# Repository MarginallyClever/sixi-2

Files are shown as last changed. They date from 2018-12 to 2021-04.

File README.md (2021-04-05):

# Sixi 2 Robot Arm

Sixi 2 is an open source industrial robot arm.  It is designed with six degrees of freedom and can hold 2kg at 80cm.
Some examples of it in action:



## Videos

* https://www.instagram.com/p/B56L99UnWkN/
* https://www.instagram.com/p/B6L7YMTnthS/
* https://www.instagram.com/p/B6jtXw5HbRo/

## Motivation

3D printers can print parts for themselves, but they cannot self-assemble.  The long goal of the Sixi is to build a machine that can assemble copies of itself.

When 3D printers were closed source, they started at $10k.  Makerbot and Prusa changed the game by bringing high quality open source 3D printers down to $2k.  Marginally Clever Robots, Ltd. aims to be the Prusa of robot arms.

## This repository 

This repository contains:

* The STL files from the stable version
* The bill of materials (BOM.csv)
* Issue tickets specifically related to the hardware.
* ROS package.

This repository does NOT contain:

* Assembly instructions + software guide: https://mcr.dozuki.com/c/Sixi_2_kit_Asssembly
* Robot Overlord app to simulate, drive, and test Sixi: https://github.com/MarginallyClever/Robot-Overlord-App
* Makelangelo Firmware in the Sixi's brain: https://github.com/MarginallyClever/Makelangelo-firmware

## Notes

The BOM.csv lists all the parts in the kit, most of which are off-the-shelf.  Some parts are manufactured.
	
	[LSR] laser cut
	[CNC] metal cut on a CNC mill
	[3D]  3D printed PLA plastic.

All the 3D printable parts were produced on a Prusa MK3S.  Parts are carefully designed to have a minimum of support material cleaning.
Please see STLs/STLPrintSettings.csv for recommended layer height, speed, color, etc.

The Sixi has no glue because we like operations that can be undone.

## Collaborate

We love collaborating!  Let's make great things happen together.

* Discuss the project in our Discord: https://discord.gg/p2NRZFxXbh
* For a link to the Fusion files, become one of our Patreon supporters: https://www.patreon.com/imakerobots
* See also the ROS.org wiki page: https://wiki.ros.org/Robots/Sixi

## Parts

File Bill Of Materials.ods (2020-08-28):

SKU | Part name | Image | type | Qty per Sixi | Unit | Buy Link | Alt buy link | Cost | Currency
Sixi2-001 | Standoff m4x6x20 95947A056 | https://imgur.com/KX3Rz3N | fastener | 16 |  | https://www.aliexpress.com/item/33029121480.html |  | $7.58 | cad
Sixi2-002 | Standoff m3x4.5x12 95947A008 | https://imgur.com/IH3mTjJ | fastener | 7 |  | https://www.aliexpress.com/item/33029121480.html |  | $2.85 | cad
Sixi2-003 | Standoff #4-40x7 M-F 93505A101 | https://imgur.com/c1Dago8 | fastener | 4 |  | https://www.mcmaster.com/93505A101
Sixi2-005 | Set Screw m3x4 flatEnd 92605A098 | https://www.mcmaster.com/mvb/library/20130930/92605a098l.gif | fastener | 22 |  | https://www.aliexpress.com/item/32864937826.html
Sixi2-009 | screw M5x20 socket head cap 90128A248 | https://www.mcmaster.com/mvb/library/20140217/90128a248l.gif | fastener | 12 |  | https://www.mcmaster.com/90128a248
Sixi2-012 | screw M4x45 socket head cap partially threaded 91292A133 | https://www.mcmaster.com/mvb/library/20140512/91292a133l.gif | fastener | 36 |  | https://www.mcmaster.com/91292A133
Sixi2-014 | screw M4x25 socket head 91292A122 | https://imgur.com/v1CkgbG | fastener | 28 |  | https://www.mcmaster.com/91292A122 |  | $9.94 | usd
Sixi2-015 | screw M4x14 socket head cap 91292A038 | https://www.mcmaster.com/mvb/library/20140512/91292a038l.gif | fastener | 6 |  | https://www.mcmaster.com/91292a038
Sixi2-016 | screw m3x8 socket head cap 91292A112 | https://www.mcmaster.com/mvb/library/20140512/91292a112l.gif | fastener | 38 |  | https://www.mcmaster.com/91292a112
Sixi2-021 | screw m3x5 socket head cap 91292A110 | https://www.mcmaster.com/mvb/library/20140512/91292a110l.gif | fastener | 42 |  | https://www.mcmaster.com/91292a110
Sixi2-024 | screw m3x45 socket head cap partially threaded 91290A079 | https://imgur.com/NSbllIR | fastener | 59 |  | https://www.mcmaster.com/91290a079 |  | $7.58 | usd
Sixi2-029 | screw m3x35 socket head cap partially threaded 91292A033 | https://www.mcmaster.com/mvb/library/20140512/91292a033l.gif | fastener | 8 |  | https://www.mcmaster.com/91292a033
Sixi2-031 | screw m3x30 socket head cap partially threaded 91292A022 | https://www.mcmaster.com/mvb/library/20140512/91292a022l.gif | fastener | 4 |  | https://www.mcmaster.com/91292a022
Sixi2-033 | screw m3x25 socket head cap partially threaded 91292A020 | https://imgur.com/angOEbH | fastener | 47 |  | https://www.mcmaster.com/91292a020 |  | $7.23 | usd
Sixi2-037 | screw m3x20 socket head cap 91290A123 | https://imgur.com/wMKXFRN | fastener | 28 |  | https://www.mcmaster.com/91292a123 |  | $6.78 | usd
Sixi2-039 | screw m3x16 socket head cap 91292A115 | https://imgur.com/oTCz141 | fastener | 26 |  | https://www.mcmaster.com/91292a115
Sixi2-043 | screw M3x10 socket head cap 91292A113 | https://imgur.com/oTCz141 | fastener | 46 |  | https://www.mcmaster.com/91292a113
Sixi2-047 | screw m2x6 socket head cap 91292A831 | https://imgur.com/oTCz141 | fastener | 52 |  | https://www.mcmaster.com/91292a831
Sixi2-053 | screw m2x12 socket head cap 91292A834 | https://imgur.com/oTCz141 | fastener | 8 |  | https://www.mcmaster.com/91292a834
Sixi2-056 | nut m5 nylock 90576A104 | https://imgur.com/oTCz141 | fastener | 4 |  | https://www.mcmaster.com/90576a104
Sixi2-057 | nut M5 hex 90592A095 | https://imgur.com/oTCz141 | fastener | 20 |  | https://www.mcmaster.com/90592a095
Sixi2-059 | nut m4 nylock 90576A103 | https://imgur.com/oTCz141 | fastener | 10 |  | https://www.mcmaster.com/90576a103
Sixi2-061 | nut M4 hex 90592A090 | https://imgur.com/oTCz141 | fastener | 32 |  | https://www.mcmaster.com/90592a090
Sixi2-063 | nut M3 square DIN 562 | https://imgur.com/oTCz141 | fastener | 30 |  | https://www.aliexpress.com/item/32875607040.html |  | $1.27 | cad
Sixi2-067 | nut m3 nylock 90576A102 | https://imgur.com/oTCz141 | fastener | 116 |  | https://www.mcmaster.com/90576a102
Sixi2-072 | nut m3 hex 90592A085 | https://imgur.com/oTCz141 | fastener | 90 |  | https://www.mcmaster.com/90592a085
Sixi2-078 | nut m2 hex 90592A075 | https://imgur.com/oTCz141 | fastener | 4 |  | https://www.mcmaster.com/90592a075
Sixi2-079 | NEMA24 100mm | https://i.imgur.com/mdeoYVg.jpg | motor | 1 |  | https://www.omc-stepperonline.com/nema-24-stepper-motor/dual-shaft-nema-24-stepper-motor-42a-4nm-566-ozin-60x60x100mm-4-wires-24hs39-4204d.html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 |  | $34.30 | usd
Sixi2-080 | NEMA23 56mm | https://i.imgur.com/GoVljdT.jpg | motor | 2 |  | https://www.omc-stepperonline.com/nema-23-stepper-motor/e-series-nema-23-stepper-motor-bipolar-1-8deg-4-8-nm-679-87oz-in-6-0a-86x86x80mm-4-wires.html |  | $23.92 | usd
Sixi2-082 | NEMA17 48mm | https://i.imgur.com/5FlxOez.jpg | motor | 2 |  | https://www.omc-stepperonline.com/nema-17-stepper-motor/nema-17-bipolar-59ncm-84oz-in-2a-42x48mm-4-wires-w-1m-cable-and-connector.html |  | $18.78 | usd
Sixi2-083 | NEMA17 39mm | https://i.imgur.com/CCPT4R4.jpg | motor | 1 |  | https://www.omc-stepperonline.com/nema-17-stepper-motor/nema-17-bipolar-45ncm-63-74oz-in-1-5a-42x42x39mm-4-wires-w-1m-cable-and-connector.html |  | $8.22 | usd
Sixi2-084 | [LSR] - ABS Junction Box [380x260x105mm] (sold as 15"x10.2"x4.13") | https://imgur.com/rg18C09 |  | 1 |  | https://www.amazon.ca/LeMotech-Waterproof-Dustproof-Universal-Enclosure/dp/B075WZZZ49 | https://www.alibaba.com/product-detail/Waterproof-electrical-box-ABS-solid-cover_60779392408.html | $63.85 | cad
Sixi2-085 | bearing flanged MF83 [3x8x3mm] | https://imgur.com/06VHik1 | bearing | 8 |  | https://www.alibaba.com/product-detail/Sixi-Package-MF83-6813-6809-6708_1600104697831.html |  | $6.85 | cad
Sixi2-086 | bearing 6813 [65x85x10mm] | https://imgur.com/hqhQNOH | bearing | 4 |  | https://www.alibaba.com/product-detail/Sixi-Package-MF83-6813-6809-6708_1600104697831.html |  | $41.32 | cad
Sixi2-088 | bearing 6809 [45x58x7mm] | https://imgur.com/XzdQ307 | bearing | 2 |  | https://www.alibaba.com/product-detail/Sixi-Package-MF83-6813-6809-6708_1600104697831.html |  | $9.93 | cad
Sixi2-089 | bearing 6708 [40x50x6mm] | https://imgur.com/bQkI64m | bearing | 4 |  | https://www.alibaba.com/product-detail/Sixi-Package-MF83-6813-6809-6708_1600104697831.html |  | $22.64 | cad
Sixi2-090 | bearing 6706 [30x37x4mm] | https://imgur.com/hUOlbzJ | bearing | 6 |  | https://www.alibaba.com/product-detail/Sixi-Package-MF83-6813-6809-6708_1600104697831.html |  | $21.66 | cad
Sixi2-092 | bearing 6702 [15x21x4mm] | https://imgur.com/hUOlbzJ | bearing | 9 |  | https://www.alibaba.com/product-detail/Sixi-Package-MF83-6813-6809-6708_1600104697831.html
Sixi2-095 | bearing 6701 [12x18x4mm] | https://imgur.com/hUOlbzJ | bearing | 16 |  | https://www.alibaba.com/product-detail/Sixi-Package-MF83-6813-6809-6708_1600104697831.html |  | $5.93 | cad
Sixi2-099 | [RAW] - Dupont Housing 7pin | https://d3s11pzv7w3h1q.cloudfront.net/wp-content/uploads/CN-DU-H07.jpg | electrical conn | 7 |  | https://www.aliexpress.com/item/33035707563.html?spm=a2g0o.cart.0.0.6c9f3c00vk0l6Z&mp=1
Sixi2-100 | [RAW] - 40-pin Ribbon Cable pitch 1.27 {4 sets of 10 pin} - [3000mm] | https://imgur.com/TS6cFpq | electrical wire | 1 |  | https://www.aliexpress.com/item/4000007978134.html |  | $12.03 | cad
Sixi2-101 | [MISC] - Timing Belt GT2-6 [400mm] | https://i.imgur.com/uhfbEJQ.jpg | timing belt | 1 |  | https://www.aliexpress.com/item/1858498241.html?spm=2114.12010612.8148356.27.54897861M6BUJx
Sixi2-102 | [MISC] - Timing Belt GT2-6 [336mm] | https://i.imgur.com/JaAKgMa.jpg | timing belt | 2 |  | https://www.aliexpress.com/item/1858543592.html?spm=2114.12010612.8148356.31.54897861M6BUJx
Sixi2-104 | [MISC] - Timing Belt GT2-6 [160mm] | https://i.imgur.com/64wMtBN.jpg | timing belt | 3 |  | https://www.aliexpress.com/item/4000034068206.html?spm=2114.12010612.8148356.33.54897861M6BUJx
Sixi2-105 | [MISC] - Braided Cable Sleeve (16mm dia) [900mm] | https://imgur.com/uPXoAG2 |  | 1 |  | https://www.aliexpress.com/item/4000279970497.html
Sixi2-106 | [MECH] - GT2 Pulley 20t-5mm | https://imgur.com/e1Oz3dD |  | 3 |  | https://www.aliexpress.com/item/32852674549.html
Sixi2-107 | [LSR] - PSU Mounting Plate - {Acrylic} |  | laser cut | 1 |  | source material: associated plastics
Sixi2-108 | [LSR] - PicassoCoverPlate - {Acrylic} |  | laser cut | 2 |  | source material: associated plastics
Sixi2-109 | [LSR] - MountingBoard [250mmx300mm] |  | laser cut | 1 |  | source material: associated plastics
Sixi2-110 | [LSR] - ForkSensSide - {Acrylic} |  | laser cut | 1 |  | source material: associated plastics
Sixi2-111 | [LSR] - ForkGBSide - {Acrylic} |  | laser cut | 1 |  | source material: associated plastics
Sixi2-112 | [ELEC] - sensor AS5147 {straight header pins on label side} | https://imgur.com/sKfHzqC |  | 1 |  | https://www.digikey.ca/en/products/detail/ams/AS5147-TS-EK-AB/5452350 |  | $108.67 | cad
Sixi2-113 | [ELEC] - sensor AS5147 {right-angle header pins on label side} |  |  | 2 |  | https://www.digikey.ca/en/products/detail/ams/AS5147-TS-EK-AB/5452350
Sixi2-114 | [ELEC] - sensor AS5147 {right-angle header pins on chip side} |  |  | 3 |  | https://www.digikey.ca/en/products/detail/ams/AS5147-TS-EK-AB/5452350
Sixi2-118 | [RAW] - Screw Terminal 4P-3.5mm |  | electrical conn | 6 |  | https://www.aliexpress.com/item/32981258851.html
Sixi2-119 | [RAW] - Screw Terminal 8p-2.54mm |  | electrical conn | 6 |  | https://www.aliexpress.com/item/32939185688.html | https://www.digikey.ca/en/products/detail/on-shore-technology-inc/OSTVN08A150/1588868 | $10.16 | cad
Sixi2-121 | [RAW] - Screw Terminal 4p-2.54mm |  | electrical conn | 1 |  | https://www.aliexpress.com/item/32939185688.html
Sixi2-122 | [RAW] - Screw Terminal 2P-5mm |  | electrical conn | 1 |  | https://www.aliexpress.com/item/32799616010.html
Sixi2-123 | [RAW] - ROCKER SWITCH W/ IEC SOCKET & FUSE HOLDER (SCREW) | https://imgur.com/jIWw7tJ |  | 1 |  | https://www.aliexpress.com/item/32957627591.html |  | $2.17 | cad
Sixi2-124 | [ELEC] - Power Supply 24V-20A | https://imgur.com/Z2UQoKd |  | 1 |  | https://www.aliexpress.com/item/33024871217.html?currency=CAD&createTmp=1&cur_warehouse=CN |  | $29.80 | cad
Sixi2-125 | [RAW] - PCB PanelAdpater | https://imgur.com/q5Lh6uE |  | 3 |  | https://oshpark.com/projects/Xrd8Wjid/order
Sixi2-126 | [RAW] - PCB MegaShield | https://imgur.com/dRTLl7Z |  | 1 |  | https://oshpark.com/projects/pKP4QArV/order
Sixi2-127 | [ELEC] - USB-B M/F Panel Mount Extension | https://imgur.com/UnHMrv1 | electrical wire | 1 |  | https://www.aliexpress.com/item/32862578019.html |  | $1.62 | cad
Sixi2-128 | [RAW] - NPN Transistor 2N2222A |  |  | 9 |  | https://leeselectronic.com/en/product/7174.html
Sixi2-129 | [RAW] - Voltage Regulator MP1584EN |  |  | 2 |  | https://www.aliexpress.com/item/32898137328.html
Sixi2-130 | [ELEC] - magnet 8x2.5mm neodynium | https://imgur.com/sKfHzqC |  | 6 |  | Comes with AS5147
Sixi2-135 | [ELEC] - D-SUB F-Conn IDC DC-37 | https://imgur.com/c1Dago8 | electrical conn | 1 |  | https://www.aliexpress.com/item/32975383933.html | https://www.digikey.ca/en/products/detail/cw-industries/CWR-281-37-0000/59402
Sixi2-136 | [RAW] - D-SUB F-Conn right-angle DC-37 | https://imgur.com/c1Dago8 | electrical conn | 1 |  | https://www.aliexpress.com/item/32507743539.html
Sixi2-137 | [ELEC] - D-SUB M/M 1m Cable DC-37 | https://imgur.com/WCuU4bf | electrical wire | 1 |  | https://www.aliexpress.com/item/4000107157121.html |  | $5.55 | cad
Sixi2-138 | [ELEC] - Stepper Driver DM556T | https://imgur.com/uFXRD0P |  | 1 |  | https://www.omc-stepperonline.com/digital-stepper-driver-18~56a-20-50vdc-for-nema-23-24-34-stepper-motor-dm556t.html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 |  | $38.16 | usd
Sixi2-139 | [ELEC] - Stepper Driver DM542T | https://imgur.com/FjPGjfd |  | 2 |  | https://www.omc-stepperonline.com/digital-stepper-driver-10-42a-20-50vdc-for-nema-17-23-24-stepper-motor-dm542t.html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 |  | $32.29 | usd
Sixi2-140 | [ELEC] - Stepper Driver DM320T | https://imgur.com/IgUOxMS |  | 3 |  | https://www.omc-stepperonline.com/digital-stepper-driver-03-22a-18-30vdc-for-nema-8-11-14-16-17-stepper-motor-dm320t.html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 |  | $20.55 | usd
Sixi2-141 | [ELEC] - Aviation GX16-8p Cable F/F - [1000mm] | https://imgur.com/eAqFwsP | electrical wire | 4 |  | https://www.aliexpress.com/item/32840461595.html?spm=2114.12010612.8148356.41.33fb6dccKnZkSS |  | $82.15 | cad
Sixi2-142 | [RAW] - Aviation GX16-8p Plug | https://imgur.com/E9g45bx | electrical conn | 4 |  | https://www.aliexpress.com/item/32865925885.html?spm=2114.12010608.0.0.47a735f2P9IyrY |  | $5.71 | cad
Sixi2-142 | [RAW] - Aviation GX16-8p Plug |  | electrical conn | 4 |  | https://www.aliexpress.com/item/32865925885.html?spm=2114.12010608.0.0.47a735f2P9IyrY
Sixi2-143 | [ELEC] - Arduino Mega 2650 | https://imgur.com/XMHnerM |  | 1 |  | https://www.aliexpress.com/item/32850843888.html |  | $11.36 | cad
Sixi2-144 | [ELEC] - 4x22AWG {M5} - [225mm] |  | assembly | 1 |  | https://leeselectronic.com/en/product/21134.html
Sixi2-145 | [ELEC] - 4x22AWG {M4} - [185mm] |  | assembly | 1 |  | https://leeselectronic.com/en/product/21134.html
Sixi2-146 | [ELEC] - 4x22AWG {M2} - [200mm] |  | assembly | 1 |  | https://leeselectronic.com/en/product/21134.html
Sixi2-147 | [ELEC] - 4x22AWG {M0/1} - [210mm] |  | assembly | 2 |  | https://leeselectronic.com/en/product/21134.html
Sixi2-148 | [ELEC] - 4x22AWG {M3} - [165mm] |  | assembly | 1 |  | https://leeselectronic.com/en/product/21134.html
Sixi2-149 | [SUB] - 2x18AWG {Switch Jumper} - [65mm] |  | assembly | 1 |  | https://leeselectronic.com/en/product/2118182.html
Sixi2-150 | [ELEC] - 2x22AWG {PSU - Small Drivers} - [335mm] |  | assembly | 1 |  | https://leeselectronic.com/en/product/22304.html
Sixi2-151 | [ELEC] - 2x22AWG {PSU - Arduino} - [420mm] |  | assembly | 1 |  | https://leeselectronic.com/en/product/22304.html
Sixi2-152 | [ELEC] - 2x18AWG {PSU - Big Drivers} - [160mm] |  | assembly | 1 |  | https://leeselectronic.com/en/product/2118182.html
Sixi2-154 | [RAW] - 3x16AWG Power Cord - 365mm {Switch to PSU} |  | electrical wire | 1 |  | https://leeselectronic.com/en/product/27773.html
Sixi2-155 | [ELEC] - 6-pin Ribbon Cable F/O - Brown to Blue {sensor 2 Elbow} - [890mm] |  | assembly | 1 |  | https://leeselectronic.com/en/product/2287.html
Sixi2-156 | [ELEC] - 6-pin Ribbon Cable F/O - Brown to Blue {sensor 1 Shoulder} - [365mm] |  | assembly | 1 |  | https://leeselectronic.com/en/product/2287.html
Sixi2-157 | [ELEC] - 6-pin Ribbon Cable F/F - Brown to Blue {sensor 5 Hand Ext.} - [210mm] |  | assembly | 1 |  | https://leeselectronic.com/en/product/2287.html
Sixi2-158 | [ELEC] - 6-pin Ribbon Cable F/O - Brown to Blue {sensor 4 Wrist} - [1520mm] |  | assembly | 1 |  | https://leeselectronic.com/en/product/2287.html
Sixi2-159 | [ELEC] - 6-pin Ribbon Cable M/O - Brown to Blue {sensor 5 Hand} - [1470mm] |  | assembly | 1 |  | https://leeselectronic.com/en/product/2287.html
Sixi2-160 | [ELEC] - 6-pin Ribbon Cable F/O - Brown to Blue {sensor 0 Anchor} - [145mm] |  | assembly | 1 |  | https://leeselectronic.com/en/product/2287.html
Sixi2-161 | [ELEC] - 6-pin Ribbon Cable F/O - Brown to Blue {sensor 3 Ulna} - [1160mm] |  | assembly | 1 |  | https://leeselectronic.com/en/product/2287.html
Sixi2-162 | [CNC] - Tube Brass [7/32in x 492mm] | https://imgur.com/Z13f9Rq | cnc | 1 |  |  |  | $7.95 | cad
Sixi2-163 | [CNC] - Tube Brass [7/32in x 25.95mm] {wrist shaft} | https://imgur.com/1g44VEV | cnc | 1
Sixi2-164 | [CNC] - Tube Brass [5/16in x 452.6mm] | https://imgur.com/VDGTeUY | cnc | 1 |  |  |  | $10.99 | cad
Sixi2-165 | [CNC] - Tube Brass [5/16in x 19.5mm] {hand shaft} | https://imgur.com/DENvd4o | cnc | 1
Sixi2-166 | [CNC] - Tube Brass [3/8in x 76.5mm] {wrist sensor shaft} | https://imgur.com/8zaq0Lm | cnc | 1 |  |  |  | $12.50 | cad
Sixi2-167 | [CNC] - Tube Brass [3/8in x 396.35mm] | https://imgur.com/YqrMDTm | cnc | 1
Sixi2-168 | [CNC] - Tube Brass [1/8in x 520mm] {ulna sensor shaft} | https://imgur.com/7tEXEqR | cnc | 1 |  |  |  | $5.25 | cad
Sixi2-169 | [CNC] - Tube Brass [1/8in x 35mm] {hand sensor shaft} | https://imgur.com/Fj52HuV | cnc | 1
Sixi2-170 | [CNC] - Pipe Aluminum [1.375in x 360.25mm] | https://imgur.com/DYVS192 | cnc | 1 |  |  |  | $23.13 | cad
Sixi2-171 | [CNC] - Pipe Aluminum [1.375in x 260.25mm] | https://imgur.com/Qf2uR6f | cnc | 1 |  |  |  | $16.69 | cad
Sixi2-172 | dowel pin steel 91595A130 - [3x24mm] | https://imgur.com/OpPEaqS | fastener | 77 |  | https://www.aliexpress.com/item/4000176913597.html |  | $12.30 | cad
Sixi2-174 | [CNC] - Tube Brass [3.5mm x 18.5mm] {GB inner rollers} | https://imgur.com/ebuiq8H | cnc | 24 |  |  |  | $4.45 | cad
Sixi2-176 | [3D] - xSAb-AS5147 SensorAdapter2.stl |  | 3d printed | 3
Sixi2-179 | [3D] - xSAa-AS5147 SensorAdapter1.stl |  | 3d printed | 2
Sixi2-181 | [3D] - 7E-plug wall adapter.stl |  | 3d printed | 1
Sixi2-182 | [3D] - 7Db-ArduinoTray.stl |  | 3d printed | 1
Sixi2-183 | [3D] - 7Da-ArduinoStandoff.stl |  | 3d printed | 1
Sixi2-184 | [3D] - 7C-stepperDriverAdapter 542.stl |  | 3d printed | 1
Sixi2-185 | [3D] - 7B-stepperDriverAdapter 556-542.stl |  | 3d printed | 1
Sixi2-186 | [3D] - 7A-stepperDriverAdapter 320x3.stl |  | 3d printed | 1
Sixi2-187 | [3D] - 6PI-pulleyInterior OUTPUT-64t v12.stl |  | 3d printed | 1
Sixi2-188 | [3D] - 6PE-pulleyExterior OUTPUT-63t v7.stl |  | 3d printed | 1
Sixi2-189 | [3D] - 6Md-SensorMagHolder.stl |  | 3d printed | 1
Sixi2-190 | [3D] - 6Mc-WristMagHolder v7.stl |  | 3d printed | 1
Sixi2-191 | [3D] - 6Ea-rotorTOP.stl |  | 3d printed | 1
Sixi2-192 | [3D] - 6Ea-rotorBOTT.stl |  | 3d printed | 1
Sixi2-193 | [3D] - 6Ea-HousingTOP.stl |  | 3d printed | 1
Sixi2-194 | [3D] - 6Ea-HousingBOTT.stl |  | 3d printed | 1
Sixi2-195 | [3D] - 6Ea-eShaftTOP.stl |  | 3d printed | 1
Sixi2-196 | [3D] - 6Ea-eShaftBOTT.stl |  | 3d printed | 1
Sixi2-197 | [3D] - 6Db-BevelGear OUTPUT-20t.stl |  | 3d printed | 1
Sixi2-198 | [3D] - 6Da-rotorTOP.stl |  | 3d printed | 1
Sixi2-199 | [3D] - 6Da-rotorBOTT.stl |  | 3d printed | 1
Sixi2-200 | [3D] - 6Da-outputDiskTOP.stl |  | 3d printed | 1
Sixi2-201 | [3D] - 6Da-outputDiskBOTT.stl |  | 3d printed | 1
Sixi2-202 | [3D] - 6Da-HousingTOP.stl |  | 3d printed | 1
Sixi2-203 | [3D] - 6Da-HousingBOTT.stl |  | 3d printed | 1
Sixi2-204 | [3D] - 6Da-Hand.stl DEPRECATED |  | 3d printed | 1
Sixi2-205 | [3D] - 6Da-eShaftTOP.stl |  | 3d printed | 1
Sixi2-206 | [3D] - 6Da-eShaftBOTT.stl |  | 3d printed | 1
Sixi2-207 | [3D] - 6Bc-bearingSpacer v3.stl |  | 3d printed | 1
Sixi2-208 | [3D] - 6Ba-BevelGear INPUT-20t v13.stl |  | 3d printed | 1
Sixi2-209 | [3D] - 6Ae-SensHolder.stl |  | 3d printed | 1
Sixi2-210 | [3D] - 6Ad-wristGBDiskBott.stl |  | 3d printed | 1
Sixi2-211 | [3D] - 6Ac-wristGBDiskTop.stl |  | 3d printed | 1
Sixi2-212 | [3D] - 6Ab-PicassoTop.stl |  | 3d printed | 1
Sixi2-213 | [3D] - 6Aa-PicassoBottom.stl |  | 3d printed | 1
Sixi2-214 | [3D] - 5PI - pulleyInterior INPUT-64t v7.stl |  | 3d printed | 1
Sixi2-215 | [3D] - 5PE - pulleyExterior INPUT-63t v7.stl |  | 3d printed | 1
Sixi2-216 | [3D] - 5I - Idler BearingCoverHalf.stl |  | 3d printed | 8
Sixi2-217 | [3D] - 5Bd - outputDiskTOP.stl |  | 3d printed | 1
Sixi2-218 | [3D] - 5Bd - outputDiskMID.stl |  | 3d printed | 1
Sixi2-219 | [3D] - 5Bd - outputDiskBOTT.stl |  | 3d printed | 1
Sixi2-220 | [3D] - 5Bc - housingTOP2.stl |  | 3d printed | 1
Sixi2-221 | [3D] - 5Bc - housingTOP1.stl |  | 3d printed | 1
Sixi2-222 | [3D] - 5Bb - housingMID.stl |  | 3d printed | 1
Sixi2-223 | [3D] - 5Ba - housingBOTT2.stl |  | 3d printed | 1
Sixi2-224 | [3D] - 5Ba - housingBOTT1.stl |  | 3d printed | 1
Sixi2-225 | [3D] - 5B - shaftCAP.stl |  | 3d printed | 1
Sixi2-226 | [3D] - 5B - rotorTOP.stl |  | 3d printed | 1
Sixi2-227 | [3D] - 5B - rotorBOTT.stl |  | 3d printed | 1
Sixi2-228 | [3D] - 5B - eShaftTOP.stl | https://imgur.com/RXKgI3l | 3d printed | 1
Sixi2-229 | [3D] - 5B - eShaftBOTT.stl | https://imgur.com/LiqzP7j | 3d printed | 1
Sixi2-230 | [3D] - 5Ac - CableClamp.stl | https://imgur.com/9ks011I | 3d printed | 1
Sixi2-231 | [3D] - 5Ab - UlnaSensRod.stl | https://imgur.com/0YdJMmV | 3d printed | 1
Sixi2-232 | [3D] - 5Aa - ForkTop.stl |  | 3d printed | 1
Sixi2-233 | [3D] - 5Aa - ForkBottom.stl |  | 3d printed | 1
Sixi2-234 | [3D] - 4S-Sixi spacer v8.stl | https://imgur.com/ebuiq8H | 3d printed | 1
Sixi2-235 | [3D] - 4Pe-pulley7-32in OUTPUT-30t.stl |  | 3d printed | 1
Sixi2-236 | [3D] - 4Pd-pulley5-16in OUTPUT-30t.stl |  | 3d printed | 1
Sixi2-237 | [3D] - 4Pc-pulley3-8in OUTPUT-30t.stl |  | 3d printed | 1
Sixi2-238 | [3D] - 4MB-UlnaMagBearing.stl |  | 3d printed | 1
Sixi2-239 | [3D] - 4M-UlnaMagHolder.stl |  | 3d printed | 1
Sixi2-240 | [3D] - 4B-MotorMount.stl |  | 3d printed | 3
Sixi2-241 | [3D] - 4Ab-ElbowTail.stl |  | 3d printed | 1
Sixi2-242 | [3D] - 4Aa-ElbowTail.stl |  | 3d printed | 1
Sixi2-243 | [3D] - 3R-rotorTOPScrew.stl |  | 3d printed | 1
Sixi2-244 | [3D] - 3R-rotorTOPNut.stl |  | 3d printed | 1
Sixi2-245 | [3D] - 3R-rotorBOTTScrew.stl |  | 3d printed | 1
Sixi2-246 | [3D] - 3R-rotorBOTTNut.stl |  | 3d printed | 1
Sixi2-247 | [3D] - 3Mc-ElbowMagHolderCap.stl |  | 3d printed | 1
Sixi2-248 | [3D] - 3MB-ElbowMagBearing.stl |  | 3d printed | 1
Sixi2-249 | [3D] - 3M-ElbowMagHolder.stl |  | 3d printed | 1
Sixi2-250 | [3D] - 3GB-shaftSensMid.stl |  | 3d printed | 1
Sixi2-251 | [3D] - 3GB-shaftCoupler.stl |  | 3d printed | 1
Sixi2-252 | [3D] - 3GB-shaftCap - SEN.stl |  | 3d printed | 1
Sixi2-253 | [3D] - 3GB-shaftCap - MOTT.stl |  | 3d printed | 1
Sixi2-254 | [3D] - 3GB-eShaft.stl |  | 3d printed | 1
Sixi2-255 | [3D] - 3GB-elbowTOPcap.stl |  | 3d printed | 1
Sixi2-256 | [3D] - 3GB-elbowTOP - SEN.stl |  | 3d printed | 1
Sixi2-257 | [3D] - 3GB-elbowTOP - MOT.stl |  | 3d printed | 1
Sixi2-258 | [3D] - 3GB-elbowBottCap - SEN.stl |  | 3d printed | 1
Sixi2-259 | [3D] - 3GB-elbowBottCap - MOT.stl |  | 3d printed | 1
Sixi2-260 | [3D] - 3GB-elbowBOTT - SEN.stl |  | 3d printed | 1
Sixi2-261 | [3D] - 3GB-elbowBOTT - MOT.stl |  | 3d printed | 1
Sixi2-262 | [3D] - 2R-rotorTOPScrew.stl |  | 3d printed | 1
Sixi2-263 | [3D] - 2R-rotorTOPNut.stl |  | 3d printed | 1
Sixi2-264 | [3D] - 2R-rotorBOTTScrew.stl |  | 3d printed | 1
Sixi2-265 | [3D] - 2R-rotorBOTTNut.stl |  | 3d printed | 1
Sixi2-266 | [3D] - 2MB-ShoulderMagBearing.stl |  | 3d printed | 1
Sixi2-267 | [3D] - 2M-ShoulderMagHolder.stl |  | 3d printed | 1
Sixi2-268 | [3D] - 2GB-shoulderTopCap - SEN.stl |  | 3d printed | 1
Sixi2-269 | [3D] - 2GB-shoulderTopCap - MOT.stl |  | 3d printed | 1
Sixi2-270 | [3D] - 2GB-shoulderTOP - SEN.stl |  | 3d printed | 1
Sixi2-271 | [3D] - 2GB-shoulderTOP - MOT.stl |  | 3d printed | 1
Sixi2-272 | [3D] - 2GB-shoulderBOTT - SEN.stl |  | 3d printed | 1
Sixi2-273 | [3D] - 2GB-shoulderBOTT - MOT.stl |  | 3d printed | 1
Sixi2-274 | [3D] - 2GB-shaftCoupler.stl |  | 3d printed | 1
Sixi2-275 | [3D] - 2GB-shaftCap - SEN.stl |  | 3d printed | 1
Sixi2-276 | [3D] - 2GB-shaftCap - MOT.stl |  | 3d printed | 1
Sixi2-277 | [3D] - 2GB-shaftBott.stl |  | 3d printed | 1
Sixi2-278 | [3D] - 2GB-eShaft.stl |  | 3d printed | 1
Sixi2-279 | [3D] - 1PO-pulleyAnchor OUTPUT-71t v6.stl |  | 3d printed | 1
Sixi2-280 | [3D] - 1PI-pulleyAnchor INPUT-71t v7.stl |  | 3d printed | 1
Sixi2-281 | [3D] - 1MB-AnchorMagBearing.stl |  | 3d printed | 1
Sixi2-282 | [3D] - 1M-AnchorMagHolder.stl |  | 3d printed | 1
Sixi2-283 | [3D] - 1GB-shaftTop.stl |  | 3d printed | 1
Sixi2-284 | [3D] - 1GB-shaftEccentric.stl |  | 3d printed | 1
Sixi2-285 | [3D] - 1GB-shaftBott.stl |  | 3d printed | 1
Sixi2-286 | [3D] - 1GB-rotorTOP.stl |  | 3d printed | 1
Sixi2-287 | [3D] - 1GB-rotorBOTT.stl |  | 3d printed | 1
Sixi2-288 | [3D] - 1GB-outputTopDisk.stl |  | 3d printed | 1
Sixi2-289 | [3D] - 1GB-outputTopBearing.stl |  | 3d printed | 1
Sixi2-290 | [3D] - 1GB-outputBottDiskTop.stl |  | 3d printed | 1
Sixi2-291 | [3D] - 1GB-outputBottDiskBott.stl |  | 3d printed | 1
Sixi2-292 | [3D] - 1E-M5x8mm Spacer v3.stl |  | 3d printed | 4
Sixi2-293 | [3D] - 1D-ShoulderMount.stl |  | 3d printed | 1
Sixi2-294 | [3D] - 1C-PanelMount.stl |  | 3d printed | 1
Sixi2-295 | [3D] - 1Bb-AnchorRearBottom.stl |  | 3d printed | 1
Sixi2-296 | [3D] - 1Ba-AnchorFrontBottom.stl |  | 3d printed | 1
Sixi2-297 | [3D] - 1Ab-AnchorMotorHolder.stl | https://imgur.com/8JFypvg | 3d printed | 1
Sixi2-298 | [3D] - 1Aa-AnchorTopSpacer.stl | https://imgur.com/aI7XwZJ | 3d printed | 1
Sixi2-299 | [3D] - 1Aa-AnchorTopBearing.stl | https://imgur.com/6mbvk0M | 3d printed | 1
Sixi2-300 | [3D] - 1Aa-AnchorGearBox.stl | https://imgur.com/7G8Ddya | 3d printed | 1
Sixi2-301 | [CNC] - 1PI-AnchorMotorShaftAdapter |  | cnc | 1 |  | Source material: Metal Super Market
Sixi2-302 | [ELEC] - PSU NEMA-15 power cable 8' |  | electrical wire | 1 |  | https://leeselectronic.com/en/product/17173.html
Sixi2-303 | [RAW] - Dupont Crimp Pins Male | https://a.pololu-files.com/picture/0J2474.1200.jpg?4dc0f8e99610600815a0e4e234f36ce4 | electrical conn | 6 |  | https://www.aliexpress.com/item/32800176540.html |  | $0.94 | cad
Sixi2-304 | [RAW] - Dupont Crimp Pins Female | https://a.pololu-files.com/picture/0J2472.1200.jpg?aed52aea0a6dd376369a345d987c5ad1 | electrical conn | 36 |  | https://www.aliexpress.com/item/32912119601.html |  | $2.10 | cad
Sixi2-305 | [ELEC] - 3-pin Servo Extension Cable M/F - [1000mm] |  |  | 2 |  | https://www.aliexpress.com/item/32986331693.html
Sixi2-306 | [RAW] - Acrylic Sheet {clear} [0.125"x24"x24"] |  |  | 2 |  | Associated Plastics
Sixi2-307 | [RAW] - Pipe Aluminum [1.375in x 361mm] (sold as 1-3/8" dia) |  |  | 1 |  | Metal Supermarket
Sixi2-308 | [RAW] - Pipe Aluminum [1.375in x 261mm] (sold as 1-3/8" dia) |  |  | 1 |  | Metal Supermarket
Sixi2-309 | [RAW] - Aluminum Block [51x 51 x 9.7mm] |  |  | 1 |  | Metal Supermarket
Sixi2-310 | [RAW] - Tube Brass [7/32in x 900mm] |  |  | 1 |  | Magic Box Hobbies
Sixi2-311 | [RAW] - Tube Brass [5/16in x 900mm] |  |  | 1 |  | Magic Box Hobbies
Sixi2-312 | [RAW] - Tube Brass [3/8in x 900mm] |  |  | 1 |  | Magic Box Hobbies
Sixi2-313 | [RAW] - Tube Brass [1/8in x 900mm] |  |  | 1 |  | Magic Box Hobbies
Sixi2-314 | [RAW] - Tube Brass [3.5mm x 300mm] |  |  | 2 |  | Magic Box Hobbies
Sixi2-315 | [ELEC] - 2x22AWG {Small Drivers} - [65mm] |  | assembly | 2
Sixi2-316 | [ELEC] - 2x18AWG {Big Drivers} - [110mm] |  | assembly | 2
Sixi2-317 | [ELEC] - 1x22AWG {Big Drivers} - [30mm] |  | assembly | 6
Sixi2-318 | [MISC] - Velcro Wrap [150mm] |  |  | 2 |  | https://www.aliexpress.com/item/4000916758690.html
Sixi2-319 | [ELEC] - PCB Panel Adapter {assembled} |  | assembly | 3
Sixi2-320 | [ELEC] - PCB Mega Shield {assembled} |  | assembly | 1
Sixi2-321 | [ELEC] - Aviation GX16-8p Cable M/O {TOOL} - [190mm] |  | assembly | 1
Sixi2-322 | [ELEC] - Aviation GX16-8p Cable M/O {M4-340mm & M5-310mm} |  | assembly | 1
Sixi2-323 | [ELEC] - Aviation GX16-8p Cable M/O {M2-370mm & M3-270mm} |  | assembly | 1
Sixi2-324 | [ELEC] - Aviation GX16-8p Cable M/O {M0-370mm & M1-370mm} |  | assembly | 1
Sixi2-325 | [ELEC] - Aviation GX16-8p Cable M/O - {Anchor PCB} [45mm x 2] |  | assembly | 3
Sixi2-326 | [ELEC] - Aviation GX16-8p Cable M/M {other end 4 pin dupont} - [80mm] |  | assembly | 1
Sixi2-327 | [RAW] - Sensor AS5147 |  |  | 6 |  | https://ams.com/as5147
Sixi2-328 | [RAW] - Jumper 1x2pin - 2.54mm |  | electrical conn | 3 |  | https://leeselectronic.com/en/product/2679.html
Sixi2-329 | [RAW] - Header Pins {M-straight} Single Row, pitch 2.54mm |  | electrical conn | 78 | pins | https://leeselectronic.com/en/product/21361.html
Sixi2-330 | [RAW] - Header Pins {M-straight} Double Row, pitch 2.54mm |  | electrical conn | 18 | pins | https://leeselectronic.com/en/product/21362.html
Sixi2-331 | [RAW] - Header Pins {M-right-angle} Single Row, pitch 2.54mm |  | electrical conn | 40 | pins | https://leeselectronic.com/en/product/2149.html
Sixi2-332 | [RAW] - 4x22AWG Threaded Cable [Red, Black, Green & Blue] |  | electrical wire | 1 | mm | https://leeselectronic.com/en/product/21134.html
Sixi2-333 | [RAW] - 2x22AWG Threaded Cable [Red & Black] |  | electrical wire | 1 | mm | https://leeselectronic.com/en/product/22304.html
Sixi2-334 | [RAW] - 2x18AWG Threaded Cable [Red & Black] |  | electrical wire | 1 | mm | https://leeselectronic.com/en/product/211816.html
Sixi2-335 | [RAW] - 1x22AWG Solid Cable [Black] |  | electrical wire | 1 | mm | https://leeselectronic.com/en/product/225060.html
Sixi2-336 | [ELEC] - 3x18AWG Main switch assembly |  | assembly | 1
Sixi2-337 | [RAW] - 4x18AWG Threaded Cable [Red, Black, Green & White] |  | electrical wire |  | mm | https://leeselectronic.com/en/product/211824.html
Sixi2-338 | [RAW] - Wood Sheet Birch Ply [0.125"x24"x24"] |  |  | 1 |  | Windsor Ply
Sixi2-339 | [RAW] - 6-pin Jumper Wire F/F - Brown to Blue [210mm] |  |  | 6 | pins
Sixi2-340 | [RAW] - 3d printer filament, yellow |  |  | 2 | kg | https://www.amazon.ca/1-75mm-Yellow-PLA-Printer-Filament/dp/B01CX9MOK4
Sixi2-341 | [3D] - Hand DIN EN ISO 9409-1-50-4-M6 v11 |  | 3d printed | 1

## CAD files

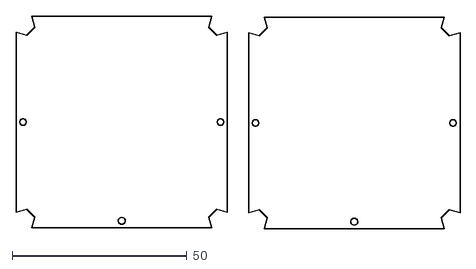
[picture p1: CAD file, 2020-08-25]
LSR/PicassoBoxCover_DXF_INKED.dxf
127.2 x 60.8

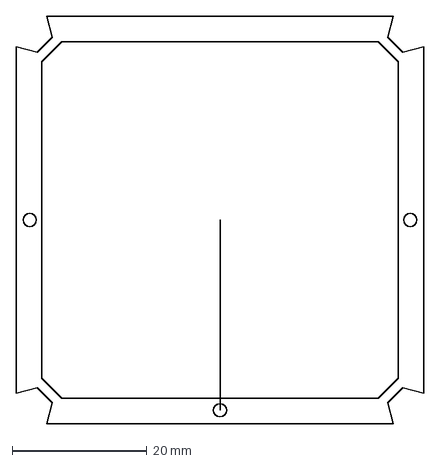
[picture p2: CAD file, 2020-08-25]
LSR/Un_INKED/PicassoBoxCover_DXF.dxf
60.6 x 60.6 mm

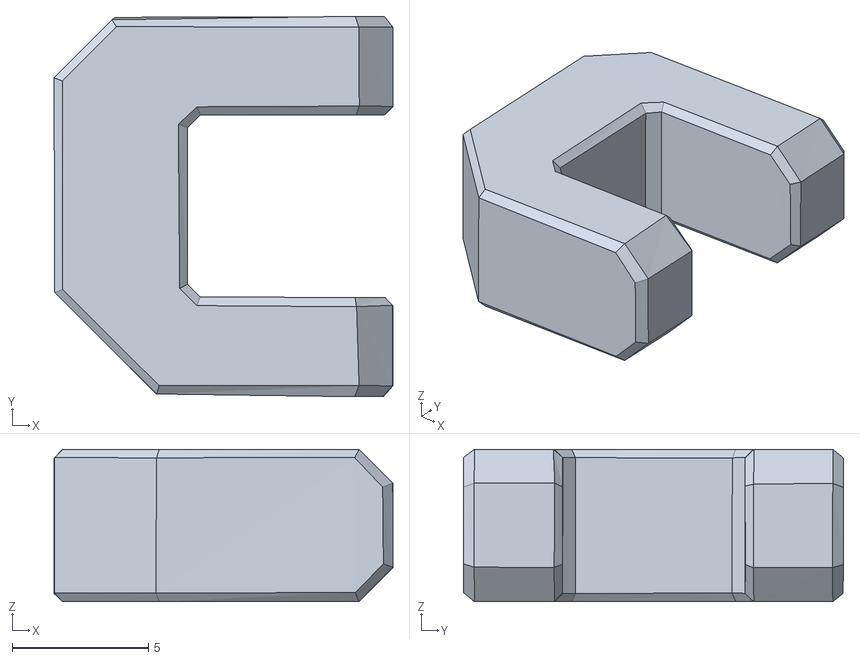
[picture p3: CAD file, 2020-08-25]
ROSPackage/meshes/5_TuningFork.obj
12.5 x 14.0 x 5.60

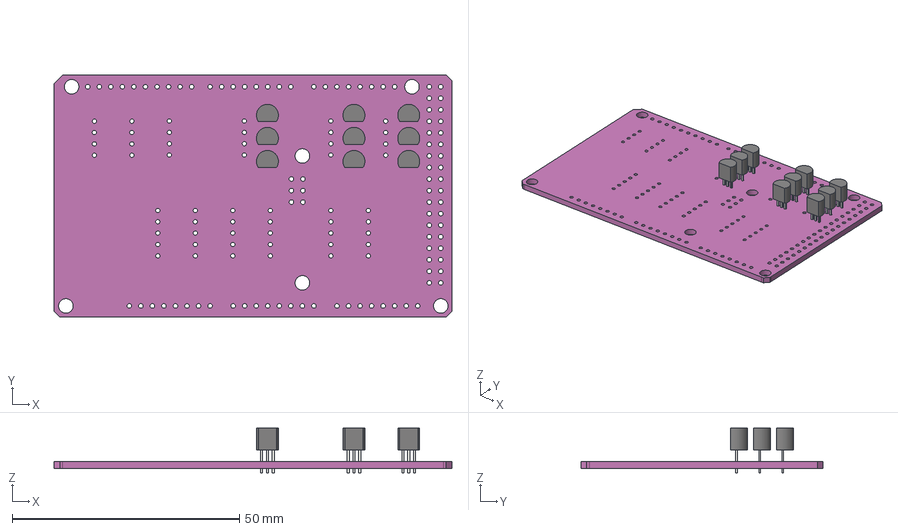
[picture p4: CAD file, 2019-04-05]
sixi2-mega-shield/sixi2-mega-shield.step
87.6 x 53.3 x 9.80 mm
Pcb
PCB_Sketch
Q30_TO-92_Inline_Narrow_5C8B03A0
Q31_TO-92_Inline_Narrow_5C8B03B2
Q32_TO-92_Inline_Narrow_5C8B03C4
Q40_TO-92_Inline_Narrow_5C8B03D6
Q41_TO-92_Inline_Narrow_5C8B03E8
Q42_TO-92_Inline_Narrow_5C8B03FA
Q50_TO-92_Inline_Narrow_5C8B040C
Q51_TO-92_Inline_Narrow_5C8B041E
Q52_TO-92_Inline_Narrow_5C8B0430

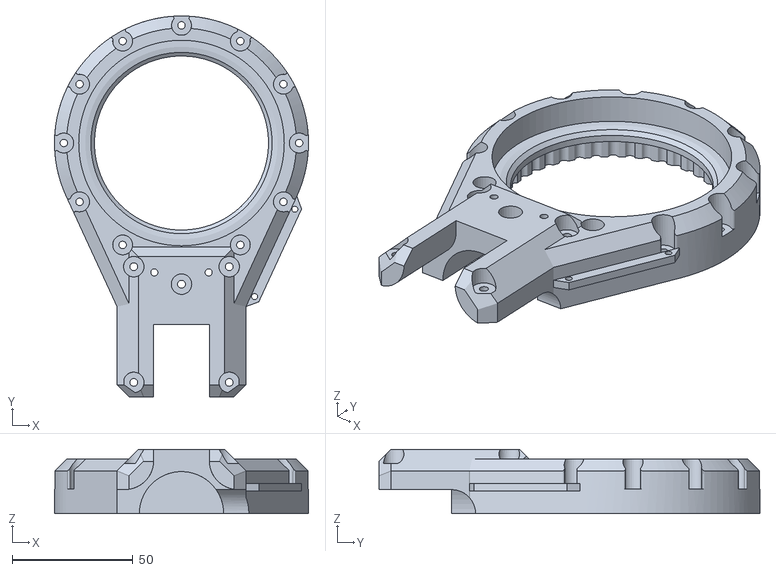
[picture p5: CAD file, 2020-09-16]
STLs/SIXI2-270 [3D] - 2GB-shoulderTOP - SEN.stl
105.2 x 157.7 x 26.7

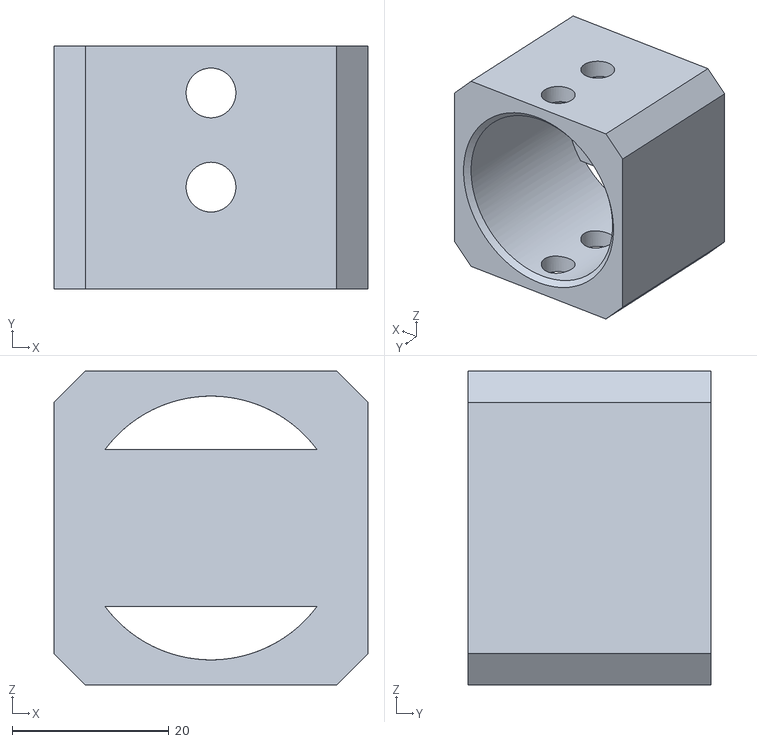
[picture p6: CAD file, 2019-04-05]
STLs/tools/pipe hole cutting jig - two hole v1.stl
40.0 x 31.0 x 40.0

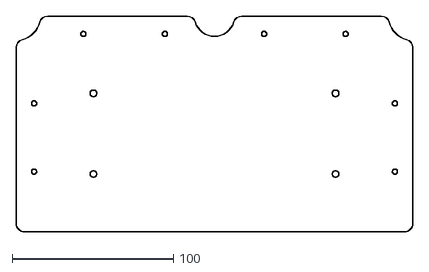
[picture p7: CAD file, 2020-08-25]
LSR/PSUMountingPlate_DXF_INKED.dxf
245.5 x 133.6

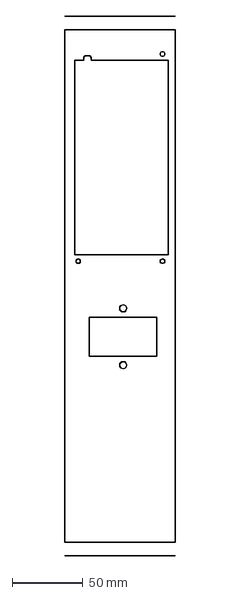
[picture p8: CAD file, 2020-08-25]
LSR/Un_INKED/CaseCut_DXF.dxf
78.0 x 380.0 mm

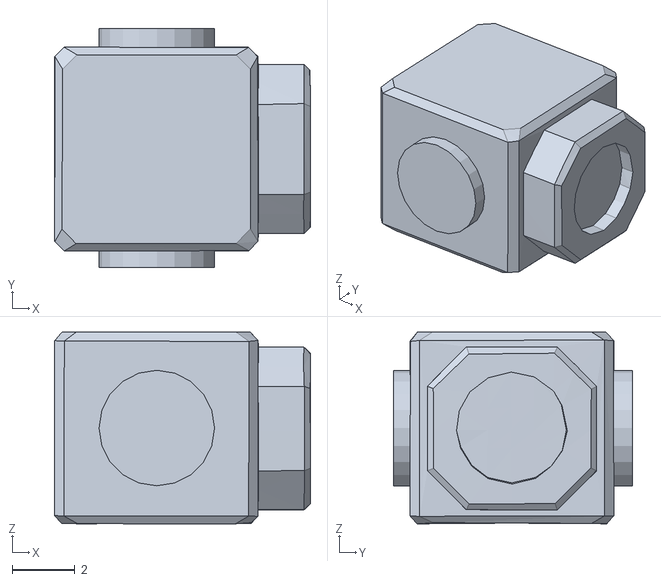
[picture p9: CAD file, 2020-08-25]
ROSPackage/meshes/6_PicassoBox.obj
8.17 x 7.61 x 6.12

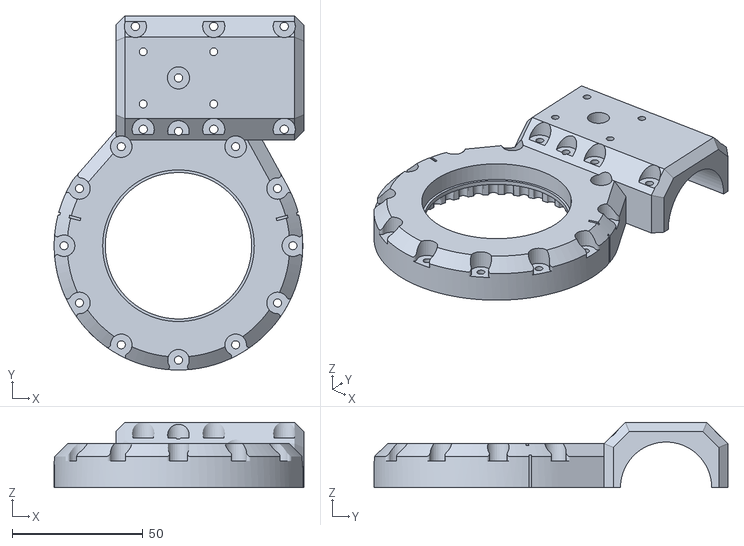
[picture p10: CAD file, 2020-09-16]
STLs/SIXI2-256 [3D] - 3GB-elbowTOP - SEN.stl
95.6 x 135.5 x 25.0

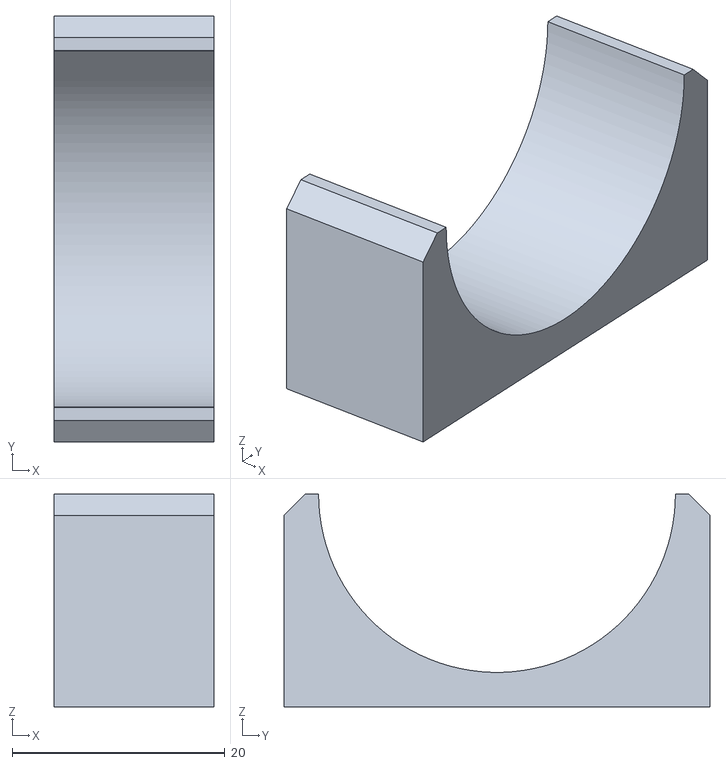
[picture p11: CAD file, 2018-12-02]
STLs/tools/1in pipe holding jig.stl
15.0 x 40.0 x 20.0

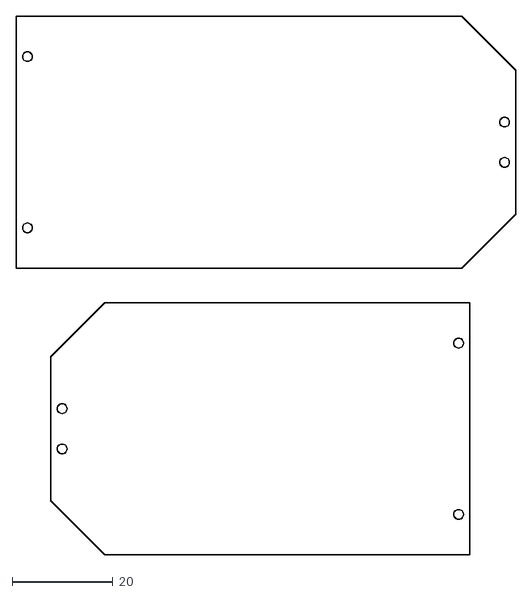
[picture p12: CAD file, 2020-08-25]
LSR/Fork_DXF_INKED.dxf
99.2 x 106.9

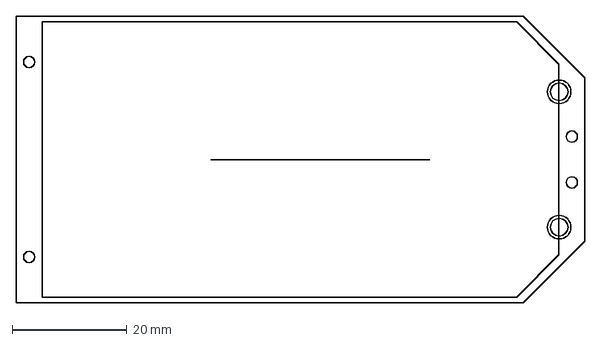
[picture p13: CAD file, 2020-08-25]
LSR/Un_INKED/ForkGearSide_DXF.dxf
99.2 x 50.0 mm

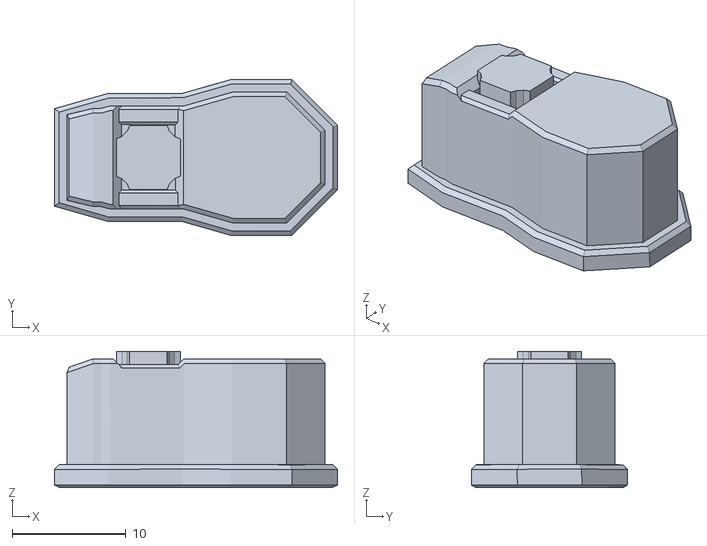
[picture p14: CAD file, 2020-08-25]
ROSPackage/meshes/1_Anchor.obj
24.9 x 13.7 x 12.0

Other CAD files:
STLs/SIXI2-219 [3D] - 5Bd - outputDiskBOTT.stl
STLs/tools/slot guide clamp.stl
LSR/CaseCut_DXF_INKED.dxf
LSR/Un_INKED/ForkSensSide_DXF.dxf
LSR/Un_INKED/PSUMountingPlate_DXF.dxf
ROSPackage/meshes/2_Shoulder.obj
ROSPackage/meshes/3_Bicep.obj
ROSPackage/meshes/4_Forearm.obj
ROSPackage/meshes/7_Hand.obj
STLs/SIXI2-176 [3D] - xSAb-AS5147 SensorAdapter2.stl
STLs/SIXI2-179 [3D] - xSAa-AS5147 SensorAdapter1.stl
STLs/SIXI2-181 [3D] - 7E-plug wall adapter.stl
STLs/SIXI2-182 [3D] - 7Db-ArduinoTray.stl
STLs/SIXI2-183 [3D] - 7Da-ArduinoStandoff.stl
STLs/SIXI2-184 [3D] - 7C-stepperDriverAdapter 542.stl
STLs/SIXI2-185 [3D] - 7B-stepperDriverAdapter 556-542.stl
STLs/SIXI2-186 [3D] - 7A-stepperDriverAdapter 320x3.stl
STLs/SIXI2-187 [3D] - 6PI-pulleyInterior OUTPUT-64t v12.stl
STLs/SIXI2-188 [3D] - 6PE-pulleyExterior OUTPUT-63t v7.stl
STLs/SIXI2-189 [3D] - 6Md-SensorMagHolder.stl
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

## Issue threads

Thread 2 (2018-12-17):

Resolve wrist pulley friction

i-make-robots, 2018-12-17:
Two belts from wrist to picasso box have trouble maintaining consistent tension and pull enough to create friction.  Supporting bearings need to be added to eliminate the friction.

Closed 2019-05-23.

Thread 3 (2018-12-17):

Motor + Brain power

i-make-robots, 2018-12-17:
Motor choice changes power requirements.
Once all power requirements are found, select and mount the appropriate power supply.

Closed 2019-05-23.

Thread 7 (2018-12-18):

Magnetic Sensor PCB Resistor and Cap. Values

jin-han, 2018-12-18:
the circuit shown in  the datasheet recommends, 48kOhms resistors, 10uF and 0.1uF capacitors.
The current circuit built has 10K resistor and 6.4uF and 0.1uF capacitors and it was tested.

The difference of these value "may" have an affect on the cleanness of data signals we are going to get. Worth following up with the recommended res. and cap. values in the future.

Closed 2019-05-23.

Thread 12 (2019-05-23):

Prevent arm from self-harm with firmware limits

i-make-robots, 2019-05-23:

i-make-robots, 2019-05-30:
Partial solution in 9be0592

i-make-robots, 2020-08-10:
firmware limits are pretty robust now.  Still possible to hit a table or itself under special conditions.

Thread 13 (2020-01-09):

Stl files are out of sync with the fusion 360 model

snarkeystarkey, 2020-01-09:
Per a discussion on Reddit, The STL files are out of date. I'm happy to see what I can do to help, if anyone has any direction they can offer. :)

i-make-robots, 2020-01-09:
The fusion 360 latest master files are in the README, and here: https://a360.co/35zKVeh

The process I follow is to hide everything except the parts in one STL file and then export the fusion root component.  That has to be repeated for each STL file.

The STL files will have a *lot* of hidden faces.  I used Blender to select all faces visible from the outside, then invert selection, then delete selection.

i-make-robots, 2020-01-09:
In a perfect world the origin of each STL file (the 0,0,0 point) is on the axis of rotation for each part.

i-make-robots, 2020-01-09:
I'm here to help and encourage in any way I can.

i-make-robots, 2020-01-13:
hey @snarkeystarkey, how is it going?  Please let me know if this still interests you and if there's any way I can help.

snarkeystarkey, 2020-01-13:
It very much does, but my free time is limited.

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

i-make-robots, 2020-02-26:
STLs have been updated and folder also contains recommended print settings.  Please help us by taking pictures of parts if you print them.  Thank you!

Closed 2020-02-26.

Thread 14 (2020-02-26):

Calibrating Magnet encoders

i-make-robots, 2020-02-26:
- [x] Match a real world grid and Sixi2 to a virtual grid and Sixi2 in Robot Overlord.  There is already a black and white 1cm grid in RO.
- [ ] Choose a robot pose P.  There must be only one valid kinematic solution to the chosen pose P.
- [ ] Make the both arms lock onto matching poses Preal & Pvirtual.  FKreal and FKvirtual should match.
- [ ] calibrate the real Sixi2 sensors until equalsEpsilon(FKreal,FKvirtual,1-e6) is true.

i-make-robots, 2020-02-27:
Tentative pose is on the side of the base, and will double as a method to secure the arm during shipping.

i-make-robots, 2020-02-27:
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
This shows possible point P.  the mounting point is build into the side of the base.  Sixi2 should probably be transported in the locked position.

i-make-robots, 2020-02-28:
Note the simulation models are long out of date and need to be brought forward to match the real machine.

i-make-robots, 2020-08-10:
Duplicate of #18

Closed 2020-08-10.

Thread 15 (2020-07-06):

Testing results of Parser.processCommand()

i-make-robots, 2020-07-06:
Wrote some code to sample the average time it takes for Parser.processCommand() to respond.  Results averaged 1500us.
Whatever lag is growing between the app and the robot is on the app side of the equation.

i-make-robots, 2020-08-10:
no longer an issue.

Closed 2020-08-10.

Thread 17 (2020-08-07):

add checks at the end of each dozuki step

i-make-robots, 2020-08-07:
"first I think it would be very useful for the future customers to set up a checking step after each motor-reductor-sensor set is installed. That way we could easily check step by step that everything goes smoothly before going to the next steps. I realized that if I did anything wrong at the beginning, it really won’t be easy to go all the way back !"

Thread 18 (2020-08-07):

Add calibration tutorial to dozuki

i-make-robots, 2020-08-07:
"I think you should make a calibration program on Robot Overlord, taking step by step the user through the calibration"

i-make-robots, 2020-08-07:
"I think that first step would be to check that we receive well all sensors and motors (easier for the sensors I must say, I don’t know how you could do it with the motors without activating them…)

second step would be to activate each motor one by one with slow mouvements, checking DOF by DOF

then for the calibration it would be like be able to move the motors one by one until the user says « I am at home position, everything is aligned ».

Then the software saves the configuration and runs everything based on that zero."

i-make-robots, 2020-08-07:
https://mcr.dozuki.com/Guide/11.+Calibrate+a+Sixi+robot/29?lang=en

i-make-robots, 2020-08-09:
https://www.marginallyclever.com/2020/08/sixi-calibration-tool/

i-make-robots, 2020-08-09:
Firmware dev branch now has D23 command to calibrate sensors.   sets home position expecting the arm is at calibration point right now.

i-make-robots, 2020-08-10:
Calibration block is fine in principle.  too close to shoulder means it does not calibrate shoulder well.

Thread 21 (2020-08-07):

swap sensors 4 & 5 on unit 1

i-make-robots, 2020-08-07:
+ update Makelangelo firmware to remove mention of SIXI_UNIT1 (now deprecated)
+ reload firmware on SIXI unit 1
+ confirm all sensors read well in R-O.

i-make-robots, 2020-08-07:
When the wires are swapped let me know and I'll do the firmware part.

jin-han, 2020-08-08:
swapped.

Closed 2020-08-08.

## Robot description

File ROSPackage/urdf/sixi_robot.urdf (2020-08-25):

<?xml version="1.0" encoding="UTF-8"?>

<robot name="sixi" xmlns:xacro="https://www.ros.org/wiki/xacro">

    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


    <link name="base_link"/>

    <link name="anchor_link">
        <origin xyz="0 0 0" rpy="0 0 0"/>
        <inertial>
            <origin xyz="0.6 0.34 0.30" rpy="0 0 0"/>
            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
            <mass value="1.0"/>
        </inertial>
        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
    </link>


    <joint name='fixed_joint' type='fixed'>
        <axis xyz="0 0 1"/>
        <origin rpy="0 0 0" xyz="0.0 0.0 0.0"/>
        <parent link="base_link"/>
        <child link="anchor_link"/>
    </joint>

    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
    <link name="shoulder_link">
        <origin xyz="0 0 -0.55" rpy="0 0 0"/>
        <inertial>
            <origin xyz="0.000181 0.187699 0.769055" rpy="0 0 0"/>
            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
            <mass value="1.0"/>
        </inertial>
        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
    </link>


    <joint name='shoulder_joint' type='revolute'>
        <axis xyz="0 0 1"/>
        <origin xyz="0 0 0.55" rpy="0 0 0"/>
        <parent link="anchor_link"/>
        <child link="shoulder_link"/>
        <limit effort="100" lower="-2.09" upper="2.09" velocity="2.9"/>
    </joint>


    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
    <link name="bicep_link">
        <origin xyz="0 0 0" rpy="0 0 0"/>
        <inertial>
            <origin xyz="0.000422 0.039042 2.038135" rpy="0 0 0"/>
            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
            <mass value="1.0"/>
        </inertial>
        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
    </link>


    <joint name='bicep_joint' type='revolute'>
        <axis xyz="0 1 0"/>
        <origin rpy="0 0 0" xyz="0.0 0.0 0.375"/>
        <parent link="shoulder_link"/>
        <child link="bicep_link"/>
        <limit effort="100" lower="-2.97" upper="0.0" velocity="2.9"/>
    </joint>

    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

    <link name="forearm_link">
        <origin xyz="0 0 0" rpy="0 0 0"/>
        <inertial>
            <origin xyz="-0.266003 -0.009119 3.766233" rpy="0 0 0"/>
            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
            <mass value="1.0"/>
        </inertial>
        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
    </link>


    <joint name='forearm_joint' type='revolute'>
        <axis xyz="0 1 0"/>
        <origin rpy="0 0 0" xyz="0.0 0.0 1.75"/>
        <parent link="bicep_link"/>
        <child link="forearm_link"/>
        <limit effort="100" lower="-1.46" upper="1.5" velocity="2.9"/>
    </joint>

    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

    <link name="tuningfork_link">
        <origin xyz="0 0 0" rpy="0 0 0"/>
        <inertial>
            <origin xyz="1.735532 0.010575 3.053760" rpy="0 0 0"/>
            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
            <mass value="1.0"/>
        </inertial>
        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
    </link>


    <joint name='tuningfork_joint' type='revolute'>
        <axis xyz="1 0 0"/>
        <origin rpy="0 0 0" xyz="1.45 0.0 0.35"/>
        <parent link="forearm_link"/>
        <child link="tuningfork_link"/>
        <limit effort="100" lower="-3.05" upper="3.05" velocity="2.9"/>
    </joint>

    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
    <link name="picassobox_link">
        <origin xyz="0 0 0" rpy="0 0 0"/>
        <inertial>
            <origin xyz="1.959861 0.000070 3.054593" rpy="0 0 0"/>
            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
            <mass value="1.0"/>
        </inertial>
        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
    </link>


    <joint name='picassobox_joint' type='revolute'>
        <axis xyz="0 1 0"/>
        <origin rpy="0 0 0" xyz="0.4 0.0 0.0"/>
        <parent link="tuningfork_link"/>
        <child link="picassobox_link"/>
        <limit effort="100" lower="-2.09" upper="2.09" velocity="2.9"/>
    </joint>

    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
    <link name="hand_link">
        <origin xyz="0 0 0" rpy="0 0 0"/>
        <inertial>
            <origin xyz="2.207627 0.000116 3.054149" rpy="0 0 0"/>
            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
            <mass value="1.0"/>
        </inertial>
        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
    </link>


    <joint name='hand_joint' type='revolute'>
        <axis xyz="1 0 0"/>
        <origin rpy="0 0 0" xyz="0.3 0.0 0.0"/>
        <parent link="picassobox_link"/>
        <child link="hand_link"/>
        <limit effort="100" lower="-2.97" upper="2.97" velocity="2.9"/>
    </joint>

    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

</robot>

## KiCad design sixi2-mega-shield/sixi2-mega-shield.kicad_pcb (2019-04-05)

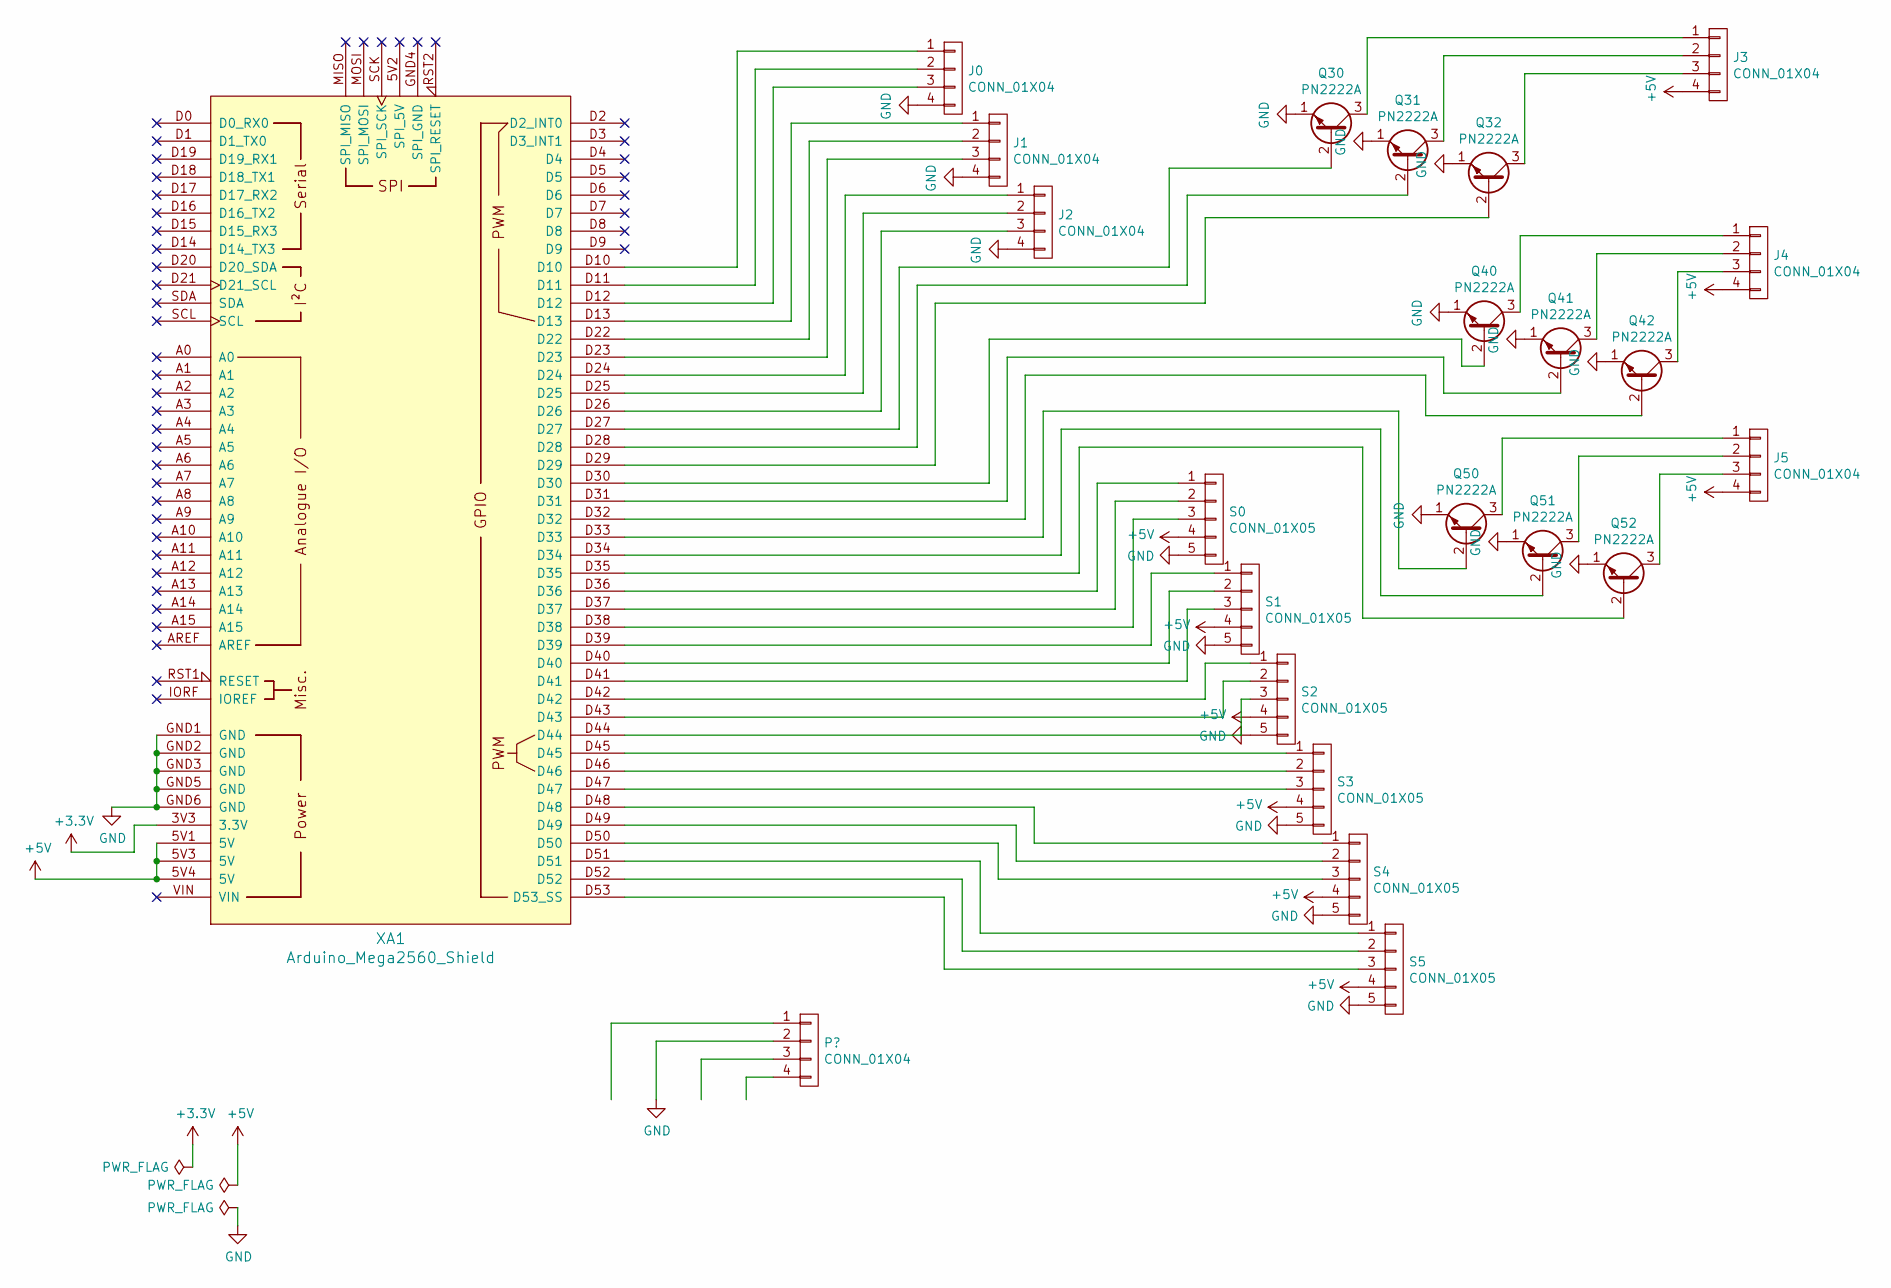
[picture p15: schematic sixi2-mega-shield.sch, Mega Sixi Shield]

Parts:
J0, J1, J2, J3, J4, J5: CONN_01X04; JST_XH_B4B-XH-A_1x04_P2.50mm_Vertical
Q30, Q31, Q32, Q40, Q41, Q42, Q50, Q51, Q52: PN2222A; TO-92_Inline_Wide
S0, S1, S2, S3, S4, S5: CONN_01X05; JST_XH_B5B-XH-A_1x05_P2.50mm_Vertical
XA1: Arduino_Mega2560_Shield

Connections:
+5V: J3.4, J4.4, J5.4, S0.4, S1.4, S2.4, S3.4, S4.4, S5.4, XA1.5V1 (5V), XA1.5V3 (5V), XA1.5V4 (5V)
GND: J0.4, J1.4, J2.4, Q30.1 (E), Q31.1 (E), Q32.1 (E), Q40.1 (E), Q41.1 (E), Q42.1 (E), Q50.1 (E), Q51.1 (E), Q52.1 (E), S0.5, S1.5, S2.5, S3.5, S4.5, S5.5, XA1.GND1 (GND), XA1.GND2 (GND), XA1.GND3 (GND), XA1.GND5 (GND), XA1.GND6 (GND)
unnamed: J0.1, XA1.D10
unnamed: J0.2, XA1.D11
unnamed: J0.3, XA1.D12
unnamed: J1.1, XA1.D13
unnamed: J1.2, XA1.D22
unnamed: J1.3, XA1.D23
unnamed: J2.1, XA1.D24
unnamed: J2.2, XA1.D25
unnamed: J2.3, XA1.D26
unnamed: J3.1, Q30.3 (C)
unnamed: J3.2, Q31.3 (C)
unnamed: J3.3, Q32.3 (C)
unnamed: J4.1, Q40.3 (C)
unnamed: J4.2, Q41.3 (C)
unnamed: J4.3, Q42.3 (C)
unnamed: J5.1, Q50.3 (C)
unnamed: J5.2, Q51.3 (C)
unnamed: J5.3, Q52.3 (C)
unnamed: Q30.2 (B), XA1.D27
unnamed: Q31.2 (B), XA1.D28
unnamed: Q32.2 (B), XA1.D29
unnamed: Q40.2 (B), XA1.D30
unnamed: Q41.2 (B), XA1.D31
unnamed: Q42.2 (B), XA1.D32
unnamed: Q50.2 (B), XA1.D33
unnamed: Q51.2 (B), XA1.D34
unnamed: Q52.2 (B), XA1.D35
unnamed: S0.1, XA1.D36
unnamed: S0.2, XA1.D37
unnamed: S0.3, XA1.D38
unnamed: S1.1, XA1.D39
unnamed: S1.2, XA1.D40
unnamed: S1.3, XA1.D41
unnamed: S2.1, XA1.D42
unnamed: S2.2, XA1.D43
unnamed: S2.3, XA1.D44
unnamed: S3.1, XA1.D45
unnamed: S3.2, XA1.D46
unnamed: S3.3, XA1.D47
unnamed: S4.1, XA1.D48
unnamed: S4.2, XA1.D49
unnamed: S4.3, XA1.D50
unnamed: S5.1, XA1.D51
unnamed: S5.2, XA1.D52
unnamed: S5.3, XA1.D53 (D53_SS)

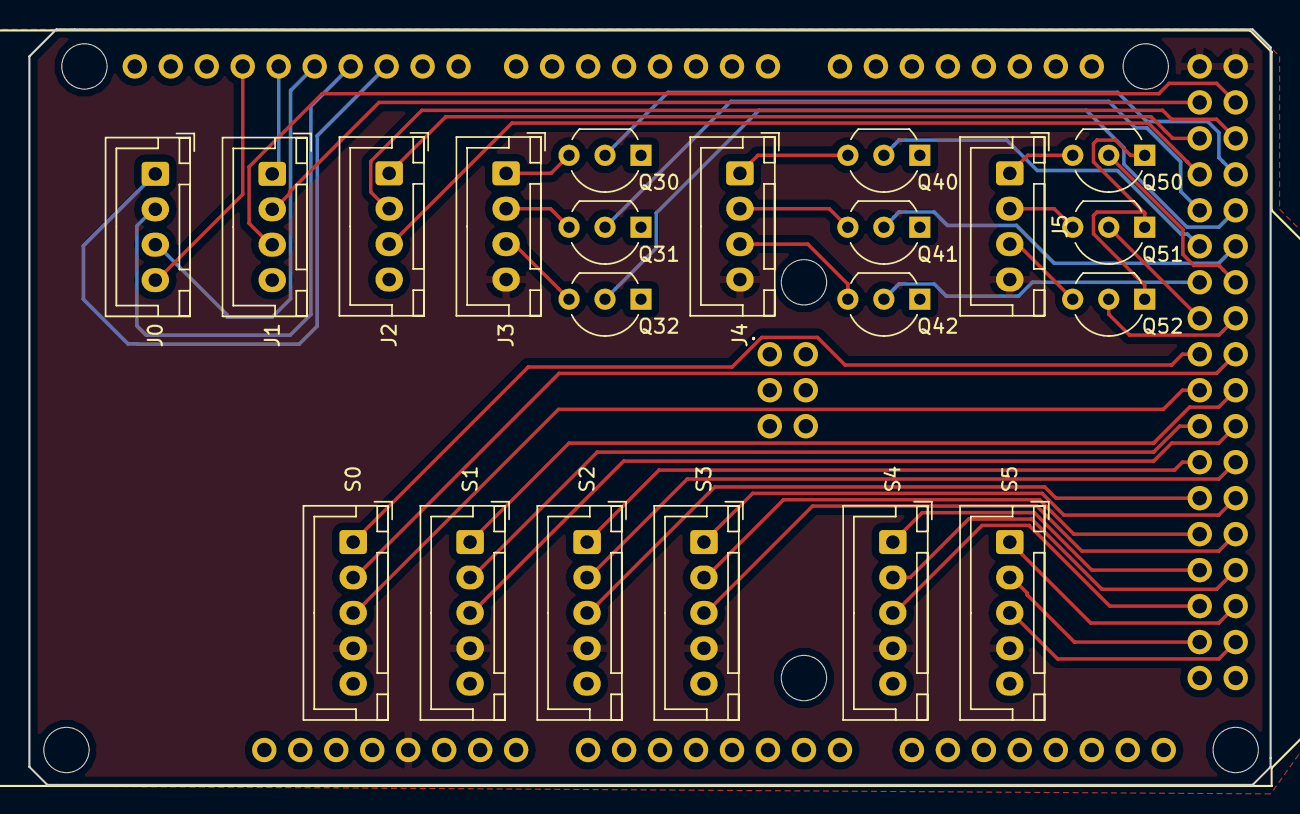
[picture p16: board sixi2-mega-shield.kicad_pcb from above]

Board: 2 copper layers, 87.6 x 53.3 mm, 22 parts (0 on the bottom side), 47 nets.

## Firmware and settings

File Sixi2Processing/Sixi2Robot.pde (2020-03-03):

enum OperatingMode {
  LIVE,
  SIM,
};

enum ControlMode {
  REAL_TIME,
  RECORD,
};


// Robot is a facade for a model-view-controller pattern.
// it controls a live robot by sending it text commands in GCODE format.
// it controls a simulated robot the exact same way.
// commands may come from any input source.  Currently these are: the joystick, the human, and the recording. 
class Sixi2Robot {
  private OperatingMode operatingMode;
  private ControlMode   controlMode;
  
  Sixi2ModelLive       modelLive;
  Sixi2ModelSimulated  modelSim;
  
  Sixi2View            view;
  RecordingView        rcView;
  
  Recording            recording;
  
  float tTotal=0;
  int selectedJoint=0;
  
  boolean singleBlock;
  boolean cycleStart;
  boolean m01break;
  
  //--------------------------------------------------------
  
  Sixi2Robot() {
    recording = new Recording();
    
    modelLive = new Sixi2ModelLive();
    modelSim = new Sixi2ModelSimulated();
    
    view = new Sixi2View();
    rcView = new RecordingView();

    operatingMode = OperatingMode.SIM;
    controlMode=ControlMode.REAL_TIME;
  }

  void reset() {
    recording.reset();
    singleBlock=false;
    cycleStart=false;
    m01break=true;
    //modelSim.sendCommand(recording.getCommand());
  }
  
  OperatingMode getOperatingMode() { return operatingMode; }
  void toggleOperatingMode() {
    operatingMode = (operatingMode==OperatingMode.LIVE) ? OperatingMode.SIM : OperatingMode.LIVE;
  }
  
  ControlMode getControlMode() { return controlMode; }
  
  void toggleControlMode() {
    controlMode = (controlMode==ControlMode.REAL_TIME) ? ControlMode.RECORD : ControlMode.REAL_TIME;
    
    if(controlMode==ControlMode.REAL_TIME) {
      // move the joystick to match the simulated position?
    }
    
    reset();
  }
  
  
  void update(float dt) {
    print(nf(tTotal,5,3)+" ");
    tTotal+=dt;
    
    Sixi2Model activeModel = null;
    switch(operatingMode) {
      case LIVE: activeModel = modelLive; break;
      case SIM : activeModel = modelSim;  break;
    }

    if(activeModel!=null) {
      if(activeModel.readyForCommands) {
        if(controlMode==ControlMode.REAL_TIME) {
          activeModel.sendCommand(modelSim.getCommand());
        } else {
          if(cycleStart && recording.hasNext()) {
            activeModel.sendCommand(recording.next());
            if(singleBlock) {
              cycleStart=false;
            }
          } else {
            cycleStart=false;
          }
        }
      }
      activeModel.update(dt);
    }
    println();
  }
  
  void render() {
    switch(operatingMode) {
      case LIVE:
        if(modelLive!=null) view.render(modelLive);
        // in live mode the sim can't be seen.
        break;
      case SIM:
        if(modelSim!=null) view.render(modelSim);
        // in sim mode, also render the live modelLive.
        if(modelLive!=null) view.render(modelLive);
        break;
    }
    
    rcView.render(recording);
  }
  
  void changePosition(float e) {
    modelSim.links[selectedJoint].angle += e;
  }
  
  // key released
  void handleInput() {
    if(key>='1' && key <='6') {
      selectedJoint = (key-'1');
    }
    
    if(key==TAB) {
      toggleControlMode();
    }
    if(key=='`' || key=='~') {
      toggleOperatingMode();
    }
  
    if(key==' ') {  // stop and reset
      reset();
    }
    if(key=='s') {
      toggleSingleBlock();
    }
    
    if(shiftPressed) {
      if((keyCode==ENTER || keyCode==RETURN)) {
        // shift+enter
        // toggle start/stop
        if(controlMode==ControlMode.RECORD) {
          toggleCycleStart();
        }
      }
    } else {
      if((keyCode==ENTER || keyCode==RETURN)) {
        // no shift + enter
        if(controlMode==ControlMode.REAL_TIME) {
          println("add command");
          recording.addCommand(modelSim.getCommand());
        }
      }
    
      if(key=='/' || key=='?') {
        recording.setCommand(modelSim.getCommand());
      }
      if(key=='+') {
        recording.addCommand(modelSim.getCommand());
      }
      
      if(key==DELETE) {
        recording.deleteCurrentCommand();
      }
      if(key==BACKSPACE) {
        recording.deletePreviousCommand();
      }
      if(key=='<' || key==',') {  // previous command
        if(recording.hasPrev()) {
          String line=recording.prev();
          modelSim.sendCommand(line);
        }
      }
      if(key=='>' || key=='.') {  // next command
        if(recording.hasNext()) {
          String line=recording.next();
          modelSim.sendCommand(line);
        }
      }
    }
  }
  
  void toggleCycleStart() {
    cycleStart = !cycleStart;
  }
  
  void toggleSingleBlock() {
    singleBlock = !singleBlock;
  }
  
  void loadRecording(String filename) {
    recording.loadRecording(filename); //<>//
  }
}

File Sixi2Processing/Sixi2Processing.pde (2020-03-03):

// 
// 2020-02-26 dan@marginallyclever.com
/*
draw blue robot, simulation.
draw yellow robot, live.

- there are two OperatingMode: simulation and live.
  - there is one Arm in each mode.
  
- there exists a DanceInstructor which demands a sequence of DanceMoves.
- an Arm is a Dancer that may subscribe to one or more a DanceInstructor(s).

The human has is a DanceInstructor. 

in mode simulation,
- yellow arm ignores all DanceInstructors.
- blue arm visuals come from SimulatedArm.

in mode live,
- blue arm ignores all DanceInstructors.
- commands are sent to the yellow arm model via Strings
- visuals are received from the blue arm model via Strings
*/


Sixi2Robot sixi2;
long tNextUpdate;
long MS_PER_UPDATE=30;


void setup() {
  size(800,800);
  sixi2 = new Sixi2Robot();
  sixi2.loadRecording("recording.txt");
  tNextUpdate=millis()+MS_PER_UPDATE;
}


void draw() {
  long tNow = millis();
  if(tNow>tNextUpdate) {
    sixi2.update((float)MS_PER_UPDATE/1000.0);
    tNextUpdate+=MS_PER_UPDATE;
  }
  
  background(128);
  sixi2.render();
}


void mouseWheel(MouseEvent event) {
  float e = event.getCount();
  sixi2.changePosition(e);
}


boolean shiftPressed=false;
void keyPressed() {
  if(keyCode==SHIFT) shiftPressed=true;
}

void keyReleased() {
  if(keyCode==SHIFT) shiftPressed=false;
  sixi2.handleInput();
}

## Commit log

2018-12-01 initial commit
    hooray!
    [1C BevelGear X4.stl, 1b sensor mount.stl, 2c sensor mount.stl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]
2018-12-02 added tools
    [1in pipe holding jig.stl, slot guide clamp.stl, slot guide section.stl]
2018-12-04 updated j3 sensor mount to include letters on part models
    [3E1 rod end holder.stl, 3d sensor mount.stl, 3s Sixi spacer.stl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]
2018-12-10 update 3Bb, added hole cut pattern for PVC tube.
    [Bb elbow mount X2.stl]
2019-04-05 Update for 2019-04-04.
    Only the kicad sixi2-mega-shield is currently valid. All other files should be treated as suspect. We are working out a new process in the workshop so that they will stay up to date all the time.
    [1C BevelGear.stl, 3C ActuatorHead.stl, Aa center wall.stl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]
2019-09-02 added graphs
    [jointVelocityOverTime.ods, workspaceBounds.ods]
2020-02-14 Updated STL files
    [1C BevelGear.stl, 1b sensor mount.stl, 2c sensor mount.stl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]
2020-02-24 STL export finalized, printsetting added
    [STLprintSetting.xlsx, [3D] - 1Ab-AnchorMotorHolder.stl, [3D] - 1Bb-AnchorRearBottom.stl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]
2020-02-26 csv version added, lsr dxf deleted,
    [STLprintSetting.csv, STLprintSetting.xlsx, [LSR] - MountingBoard 250mmx300mm.dxf]
2020-02-26 update readme and BOM
    [BOM.csv, STLprintSetting.csv, STLprintSetting.xlsx]
2020-02-26 added 089
    [BOM.csv]
2020-03-02 Turned parts for printing
    [[3D] - 1Aa-AnchorGearBox.stl, [3D] - 1Aa-AnchorTopBearing.stl, [3D] - 1Aa-AnchorTopSpacer.stl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]
2020-03-03 shoulder cut wasn't done correctly, fixed
    [[3D] - 2GB-shoulderTOP - MOT.stl]
2020-03-03 ElbowGB 3mm Roller Fixed
    [[3D] - 3GB-elbowBOTT - MOT.stl, [3D] - 3GB-elbowBOTT - SEN.stl, [3D] - 3GB-elbowBottCap - MOT.stl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]
2020-03-03 added SKUs to STL print settings file
    [STLprintSetting.csv]
2020-03-26 print setting csv file delimiter added
    [STLprintSetting.csv, printSetting.csv]
2020-07-28 added ROS package
    [1_Anchor.obj, 2_Shoulder.obj, 3_Bicep.obj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]
2020-08-25 Aug.25th STLs update
    - Notable updates
    -- Anchor Gearbox with 3mm dowel Pins
    But all STL files has been exported anew.
    [CaseCut_DXF.dxf, CaseCut_DXF_INKED.dxf, ForkGearSide_DXF.dxf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]
2020-08-25 removing old material
    [Package list.xlsx, jointVelocityOverTime.ods, workspaceBounds.ods]
2020-08-25 updated bill of materials
    [BOM.csv, Bill Of Materials.ods]
2020-08-25 Update Bill Of Materials.ods
    [Bill Of Materials.ods]
2020-08-28 update with buy-now for bearings
    [Bill Of Materials.ods]
2020-09-14 renamed STL files to include SKU codes
    [SIXI2-176 [3D] - xSAb-AS5147 SensorAdapter2.stl, SIXI2-179 [3D] - xSAa-AS5147 SensorAdapter1.stl, SIXI2-181 [3D] - 7E-plug wall adapter.stl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]
2020-09-16 rotated for printing
    [SIXI2-219 [3D] - 5Bd - outputDiskBOTT.stl, SIXI2-256 [3D] - 3GB-elbowTOP - SEN.stl, SIXI2-270 [3D] - 2GB-shoulderTOP - SEN.stl]
